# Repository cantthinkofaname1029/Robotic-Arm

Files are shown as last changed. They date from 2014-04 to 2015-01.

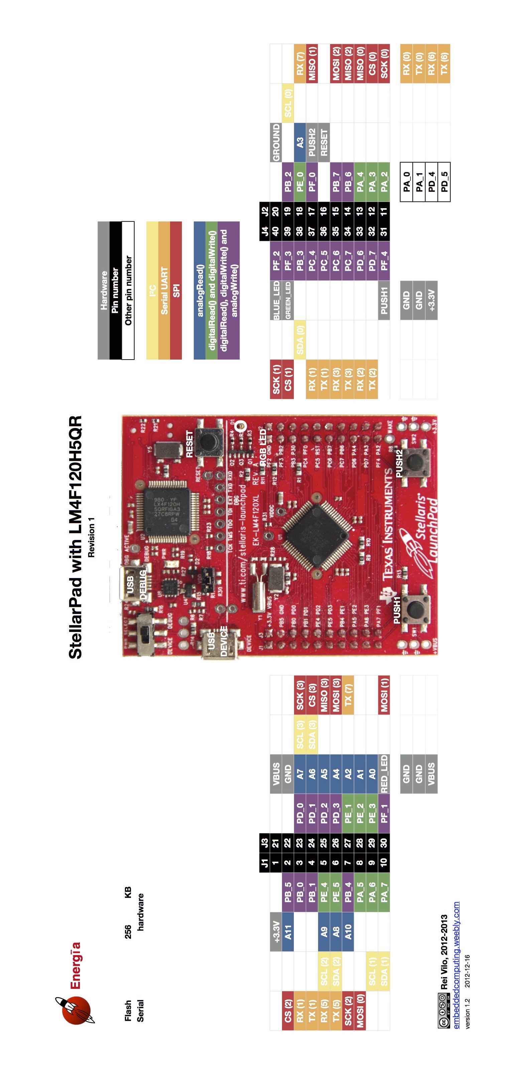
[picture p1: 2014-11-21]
hardware/v4/StellarPadLM4F120H5QR-V1.0.jpg

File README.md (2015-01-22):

Robotic Arm
===========

2015 Robotic Arm Hardware/Software
- Please see the wiki for more information about the subjects below.

Hardware:
---------

###PCBs
-Version 3 of the arm board aka "the old-new arm board" is a remake of V2 (the old arm board currently on Phoenix). It is designed to have the exact same functionality as Phoenix, without using a master-slave protocol. It features a TI Launchpad Stellaris as the central CPU, 3 motor controllers that can connect to up to two motors each, and an RS-485 connection to the old dynamixel (MX-64R). It has the additional capability of communicating with the end effector via XBee and receives power from PORN.

-Version 4 of the arm board aka "the illuminati board" is the latest version. It features a TIVA-C for it's central processor and extends the functionality of Version 3. It only has one motor controller for the Pololu actuator, but it connects to multiple Dynamixels over TTL. There is a 9DOF IMU added on the board for additional control capabilities. it also receives power from PORN.

###Motors
-The base of the arm as well as the elbow joints use the Dynamixel MX-64T. It operates at a MAXIMUM voltage of 14.8V. Information on these motors can be found here:

http://support.robotis.com/en/product/dynamixel/mx_series/mx-64.htm

http://support.robotis.com/en/techsupport_eng.htm#product/dynamixel/mx_series/mx-64.htm

http://support.robotis.com/en/techsupport_eng.htm#software/dynamixelsdk.htm

-The wrist joints on the arm use the Dynamixel MX-28T. It operates at a MAXIMUM voltage of 14.8V. Information on these motors can be found here:

http://support.robotis.com/en/product/dynamixel/mx_series/mx-28.htm

http://support.robotis.com/en/techsupport_eng.htm#product/dynamixel/mx_series/mx-28.htm

http://support.robotis.com/en/techsupport_eng.htm#software/dynamixelsdk.htm

-The shoulder joint of the arm uses a Pololu Linear Actuator with an 8" stroke and a potentiometer for feedback. It operates at a MAXIMUM of 12V. It will be controlled using an on-board motor controller. Information on this actuator can be found here:

https://www.pololu.com/product/2337/specs

Software:
---------

-Software for V3 is nearing completion. It will have basic functionality for the arm for open-loop controls.

-Software for V4 has not started yet. It will be a port from the V3 code to TivaWare.

-After the V4 code has been completed for basic functionality, we need to start writing the framework for more exotic control methods.

-There is a Dynamixel SDK found here:

http://support.robotis.com/en/software/dynamixelsdk.htm

-There is a fully-written Dynamixel Library written for Arduino here:

http://savageelectronics.blogspot.com/2011/01/arduino-y-dynamixel-ax-12.html

if you can't read spanish or use google translate, the various libraries are found here:

http://savageelectronics.blogspot.com/2011/08/actualizacion-biblioteca-dynamixel.html

These will probably be useful to us when writing the further code.

-We may have to write our own PID control for the actuator in the future. Get an introduction to PID for arduino here:

http://brettbeauregard.com/blog/2011/04/improving-the-beginners-pid-introduction/

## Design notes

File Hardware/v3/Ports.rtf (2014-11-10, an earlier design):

Motor Controller 1
Enable A PE1
A_1 PD1
A_2 PA2
Enable B PE2
B_1 PD2
B_2 PD3
Motor Controller 2
Enable A PB7
A_1 PE0
A_2 PF0
Enable B PB2
B_1 PF2
B_2 PF3
Motor Controller 3
Enable A PB6
A_1 PA3
A_2 PA4
Rovecom
RX(3) PC6
TX(3) PC7
End Effector
RX(2) PD6
TX(2) PD7
Dynamxiel
Data Control PB3
RX(1) PC4
TX(1) PC5

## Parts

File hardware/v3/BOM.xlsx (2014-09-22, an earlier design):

Name | Part Number | Type of Component | Quantity | Unit Price | Price | Company | Website
.1uF capictor |  | Passive SMD 603 | 13 |  | $0.00
1N4148 |  | Diode | 6 | $0.10 | $0.60 | Digikey | http://www.digikey.com/product-detail/en/1N4148TA/1N4148TACT-ND/1532747
5mm Terminal |  | Power Connector | 6 |  | $0.00
1kΩ |  | Passive SMD 603 | 5 |  | $0.00
5.6nF capictor |  | Passive SMD 603 | 5 | $0.10 | $0.50 | Digikey | http://www.digikey.com/product-detail/en/CL10B562KB8SFNC/1276-2092-1-ND/3890178
100kΩ resistor |  | Passive SMD 603 | 4 |  | $0.00
120Ω |  | Passive SMD 603 | 4 |  | $0.00
100Ω resistor |  | Passive SMD 603 | 3 |  | $0.00
10nF capictor |  | Passive SMD 603 | 3 | $0.10 | $0.30 | Digikey | http://www.digikey.com/product-detail/en/C0603C103K5RACTU/399-1091-1-ND/411366
220nF capictor |  | Passive SMD 603 | 3 | $0.10 | $0.30 | Digikey | http://www.digikey.com/product-detail/en/C1608X7R1H223K080AA/445-1312-1-ND/567696
Green LED |  | SMD LED | 3 | $2.95 | $2.95 | Sparkfun | https://www.sparkfun.com/products/11169
L6206D |  | IC | 3 | $10.64 | $31.92 | Digikey | http://www.digikey.com/product-detail/en/L6206D/497-3999-5-ND/725434
LTC490 |  | IC | 2 | $4.82 | $9.64 | Digikey | http://www.digikey.com/product-detail/en/LTC490CN8%23PBF/LTC490CN8%23PBF-ND/891732
Vertical RJ45 |  | Connector | 2 |  | $0.00
Red LED |  | SMD LED | 2 | $2.95 | $2.95 | Sparkfun | https://www.sparkfun.com/products/11248
XBEE Headers |  | SMD Headers | 2 | $0.95 | $1.90 | Sparkfun | https://www.sparkfun.com/products/10030
XBEE |  | Wireless | 2 | $24.95 | $49.90 | Sparkfun | https://www.sparkfun.com/products/11215
12V LDO |  | LDO | 2 | $0.70 | $1.40 | Digikey | http://www.digikey.com/product-search/en?KeyWords=MC7812BTG&WT
220Ω |  | Passive SMD 603 | 1 |  | $0.00
MAX485 |  | IC | 1 | $2.65 | $2.65 | Digikey | http://www.digikey.com/product-detail/en/MAX485CPA%2B/MAX485CPA%2B-ND/948026
Launchpad |  | Processor | 1 | $13.02 | $13.02 | Newark | http://www.newark.com/texas-instruments/ek-tm4c123gxl/eval-board-tm4c123g-tiva-c-launchpad/dp/73W9275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
XBEE Explorer |  | Wireless | 1 | $9.95 | $9.95 | Sparkfun | https://www.sparkfun.com/products/11373
18V LDO |  | LDO | 1 | $0.57 | $0.57 | Digikey | http://www.digikey.com/product-search/en?vendor=0&keywords=MC7818BTG
5V LDO |  | LDO | 1 | $0.48 | $0.48 | Digikey | http://www.digikey.com/product-detail/en/MC78M05CDTRKG/MC78M05CDTRKGOSCT-ND/1139757
3.3V LDO |  | LDO | 1 | $0.90 | $0.90 | Digikey | http://www.digikey.com/product-detail/en/MC33269DT-3.3G/MC33269DT-3.3GOS-ND/1479177
 |  |  |  |  | $129.93

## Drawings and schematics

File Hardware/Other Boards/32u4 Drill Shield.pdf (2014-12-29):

1.25

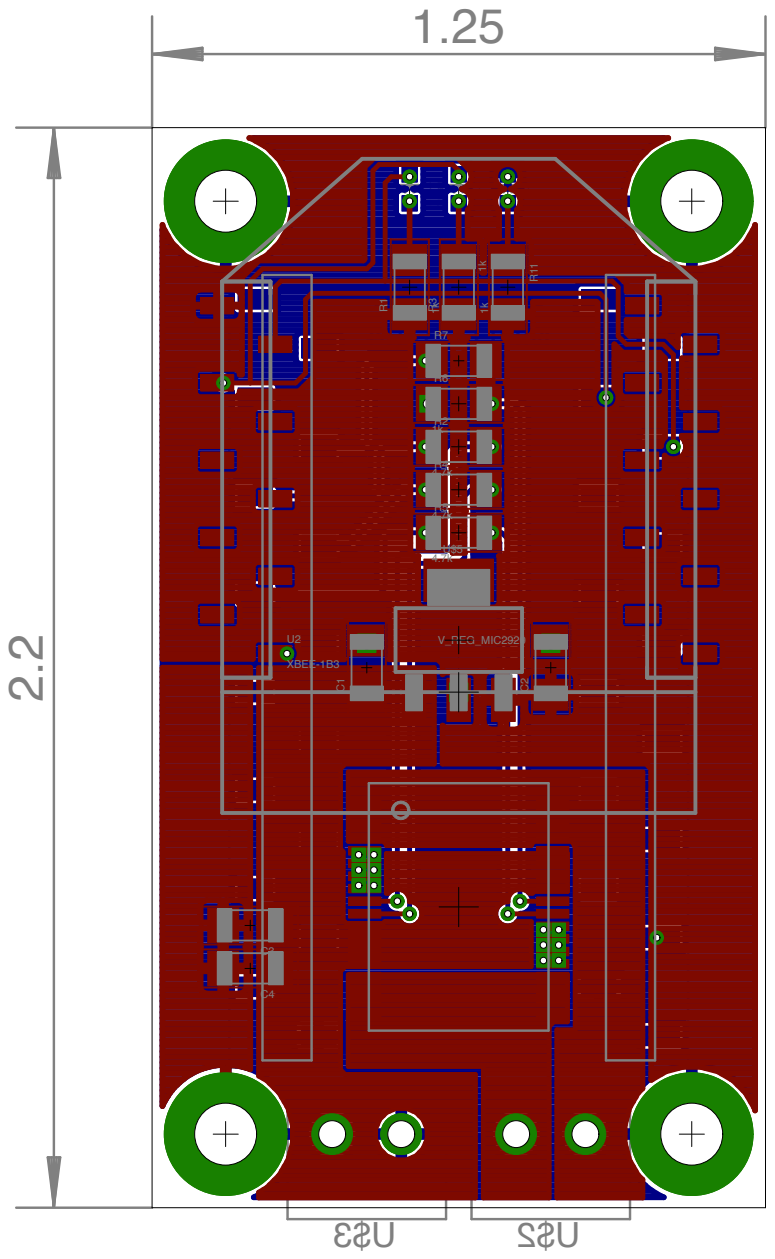
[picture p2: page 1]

R2
1k

R5
4.7k

V_REG_MIC2920

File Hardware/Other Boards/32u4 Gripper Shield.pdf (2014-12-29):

1.25

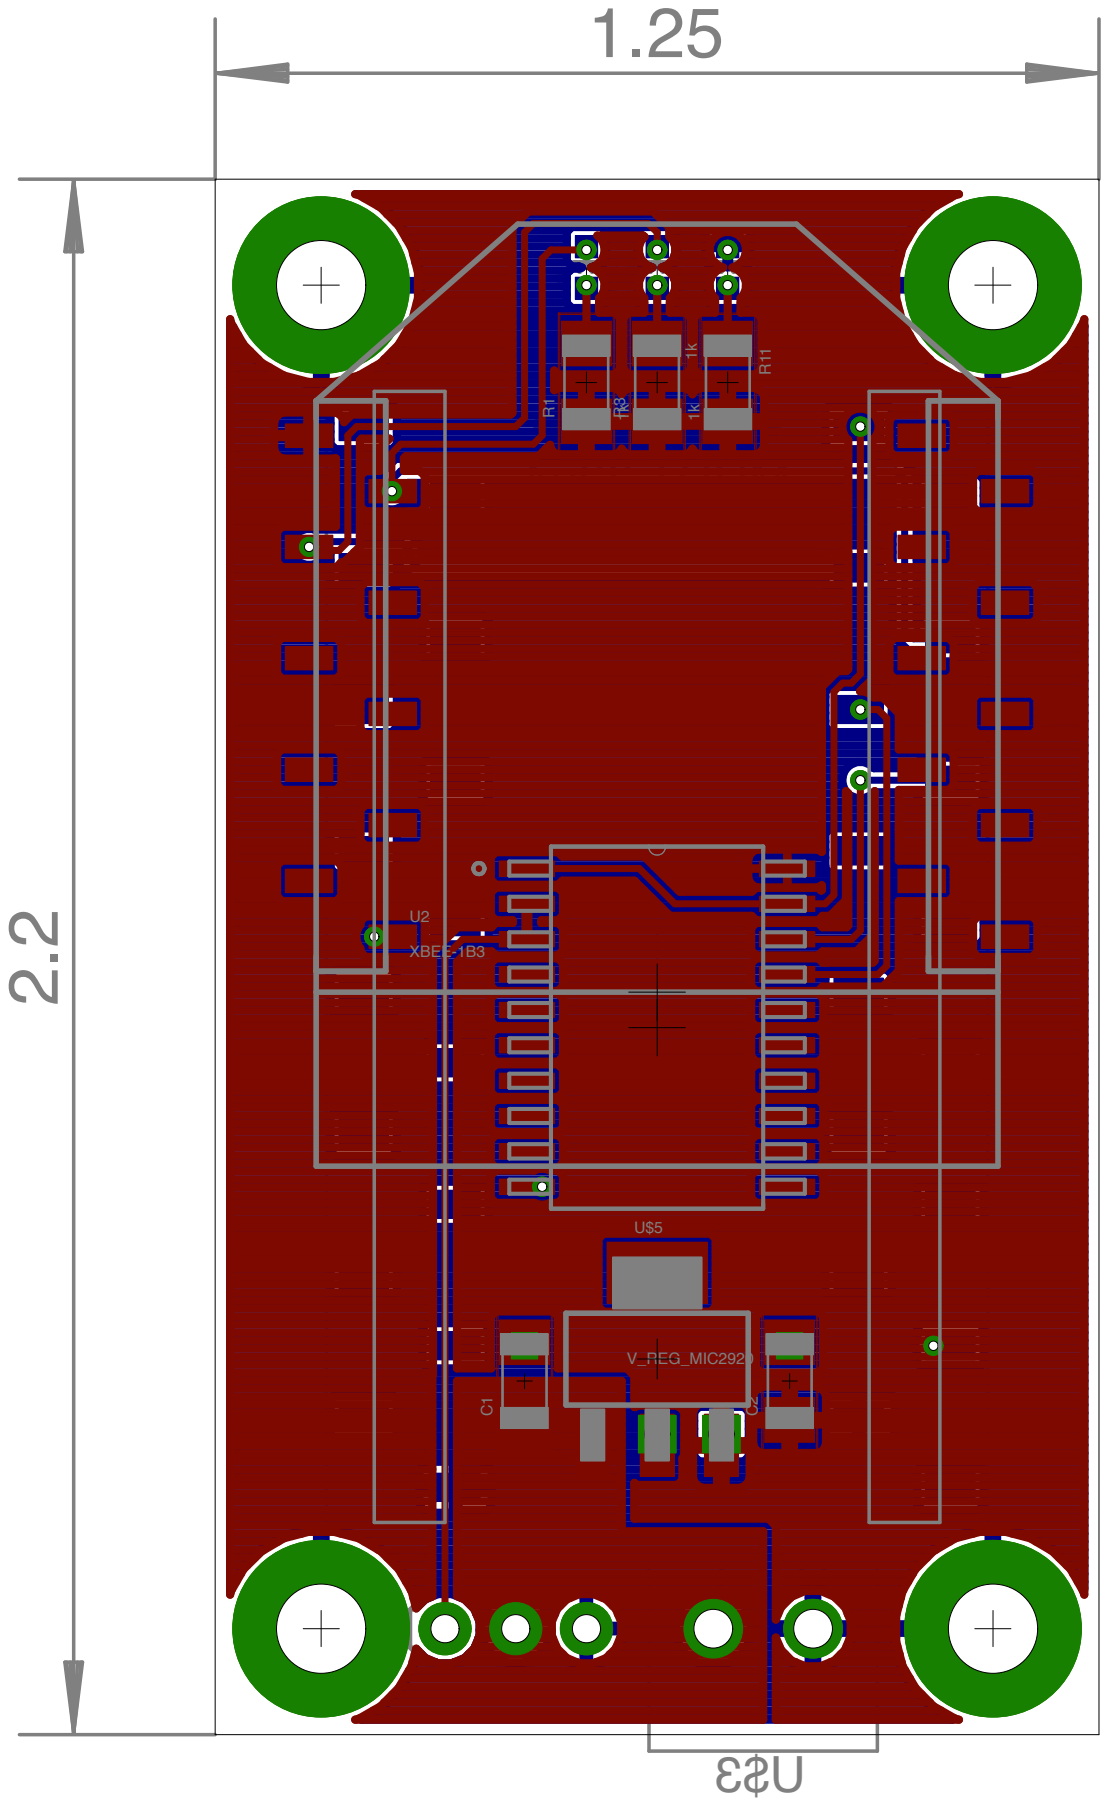
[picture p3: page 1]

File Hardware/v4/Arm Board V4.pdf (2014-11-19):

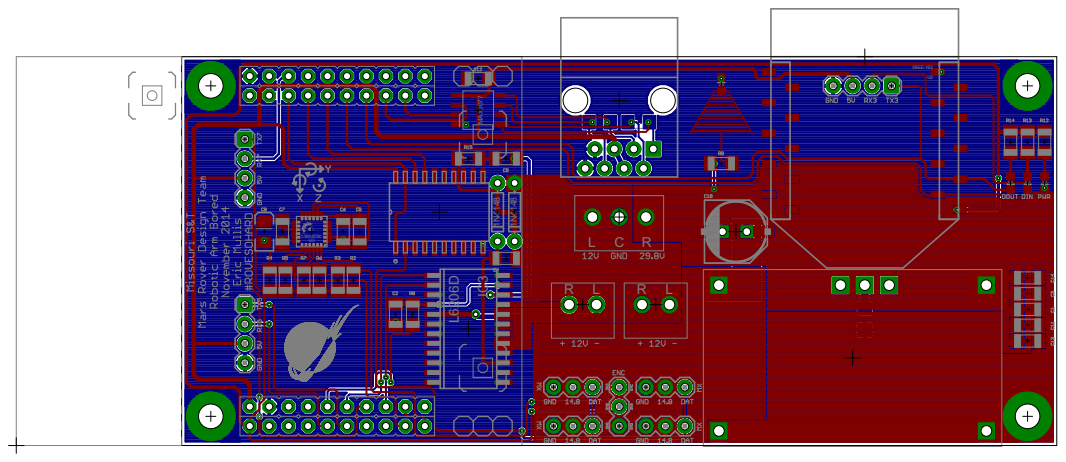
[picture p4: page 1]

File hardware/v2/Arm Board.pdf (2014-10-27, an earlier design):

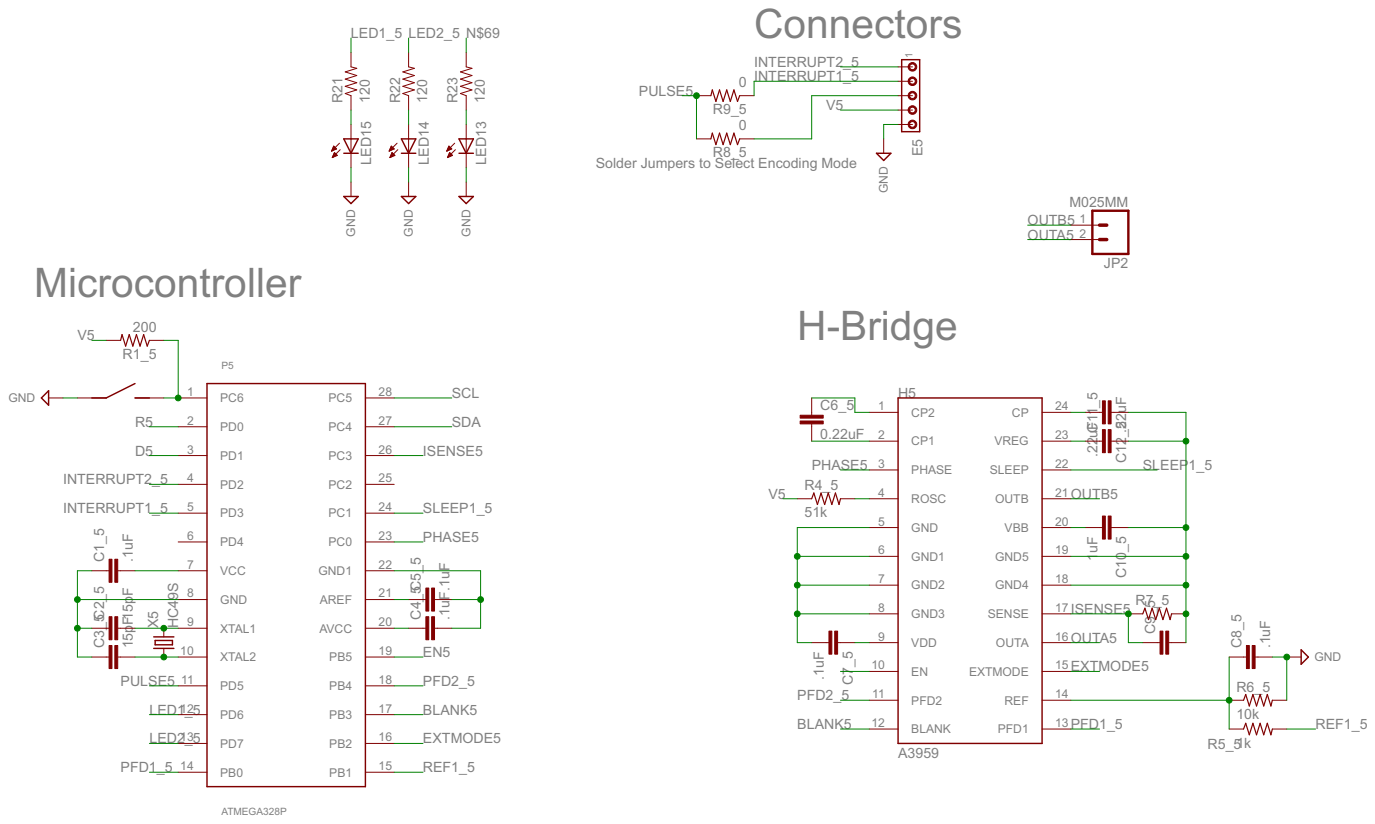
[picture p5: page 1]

Solder Jumpers to Select Encoding Mode

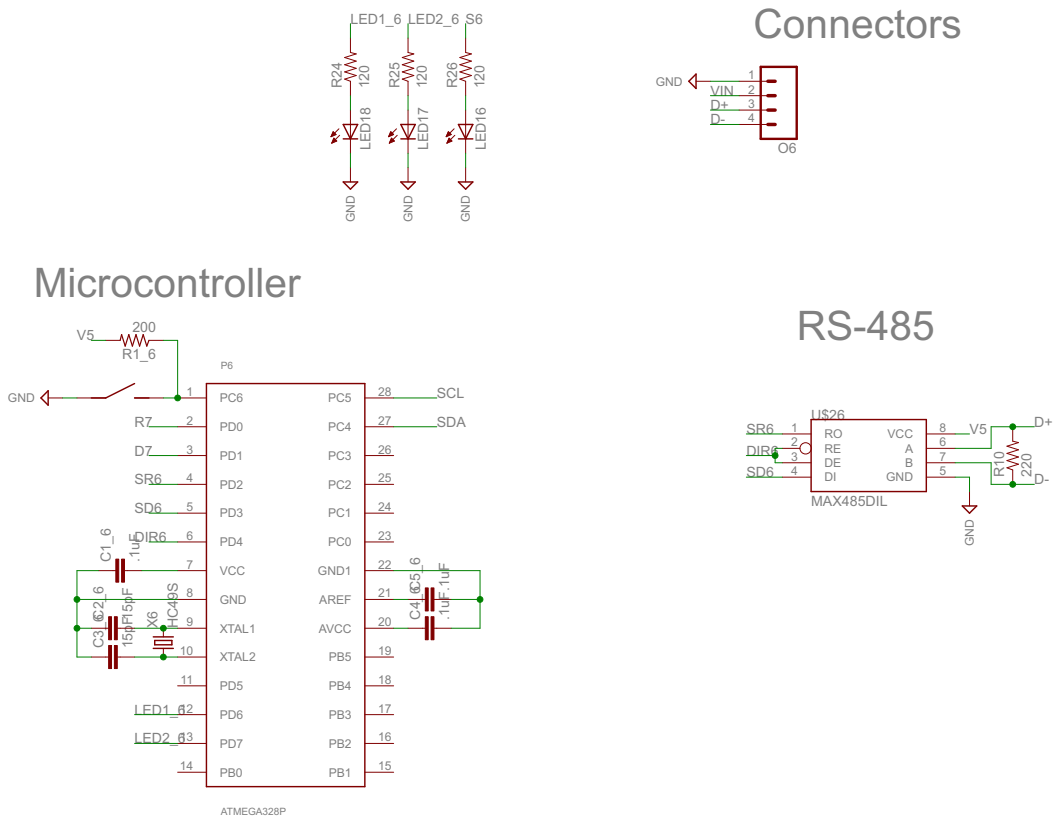
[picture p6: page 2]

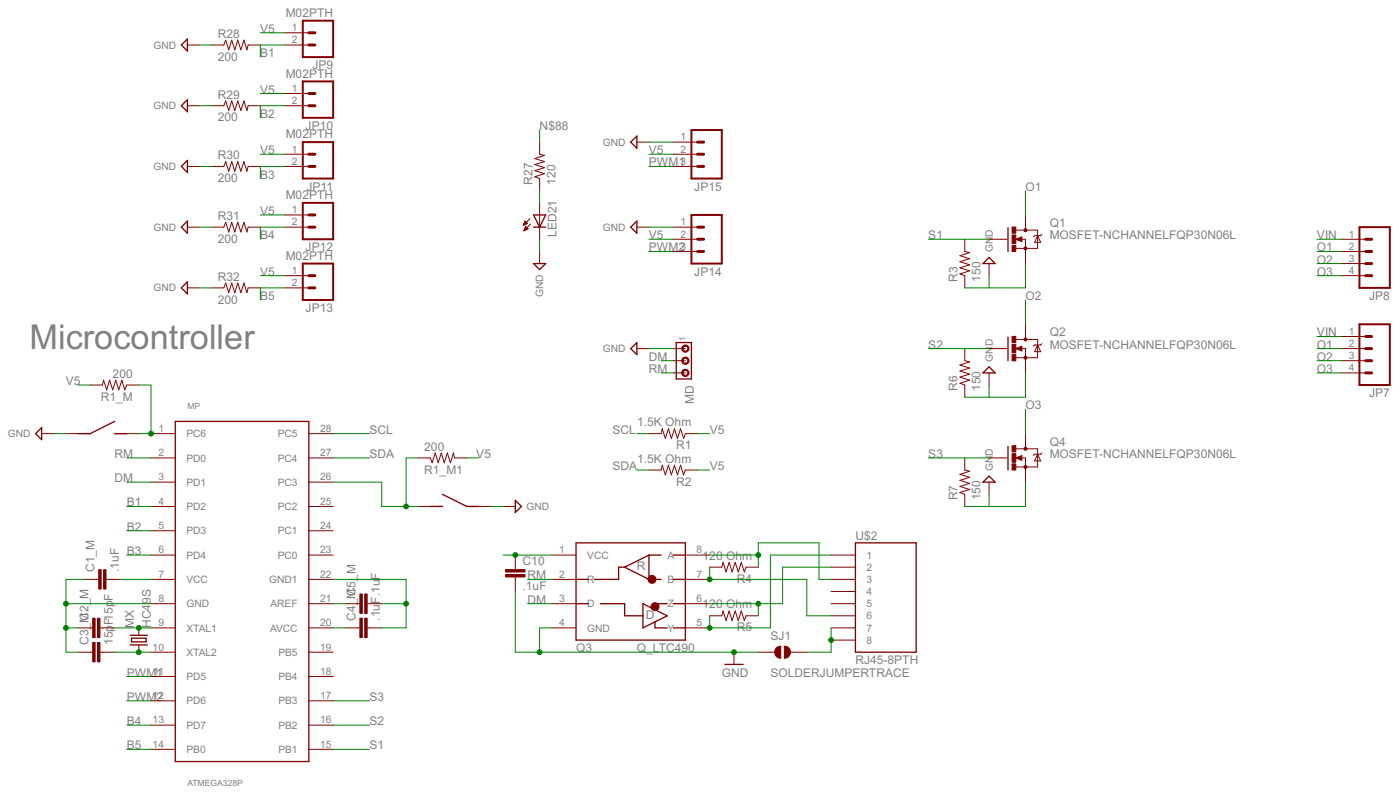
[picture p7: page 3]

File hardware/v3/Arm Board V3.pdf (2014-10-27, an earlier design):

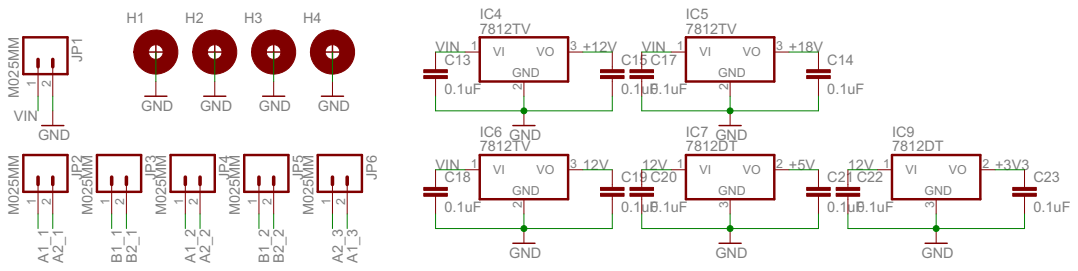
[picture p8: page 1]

M025MM GND M025MM M025MM M025MM M025MM M025MM GND GND GND GND 7812TVGND 7812TVGND 0.1uF 0.1uF0.1uF 0.1uF GND 0.1uF 0.1uF 7812TV GND 0.1uF 0.1uF 7812DT GND 0.1uF 0.1uF 7812DT JP1 12 JP2 12 JP3 12 JP4 12 JP5 12 JP6 12 H1 H2 H3 H4 IC4 GND VI 1 2 VO 3 IC5 GND VI 1 2 VO 3 C13 C15 C17 C14 C18 C19 IC6 GND VI 1 2 VO 3 C20 C21 IC7 GND VI 1 3 VO 2 C22 C23 IC9 GND VI 1 3 VO 2 A1_1 A2_1 B1_1 B2_1 A1_2 A2_2 B1_2 B2_2 A2_3 VIN VIN VIN VIN A1_3 +12V +18V 12V 12V +5V 12V +3V3

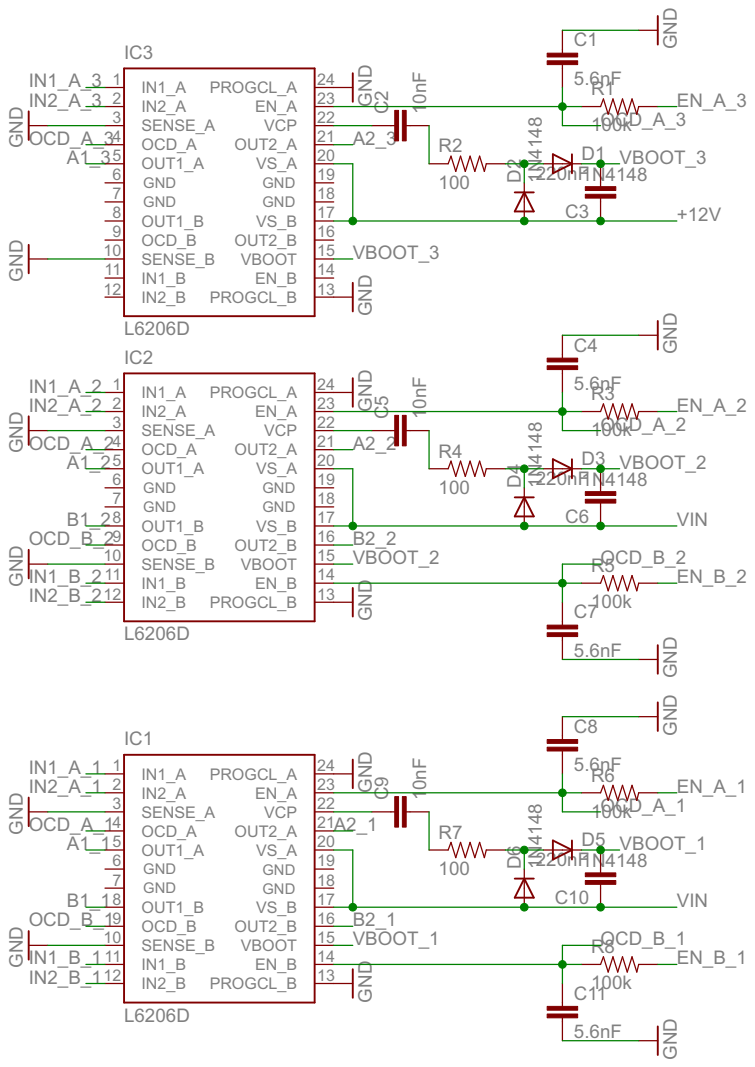
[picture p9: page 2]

GND GND
OCD_A_3

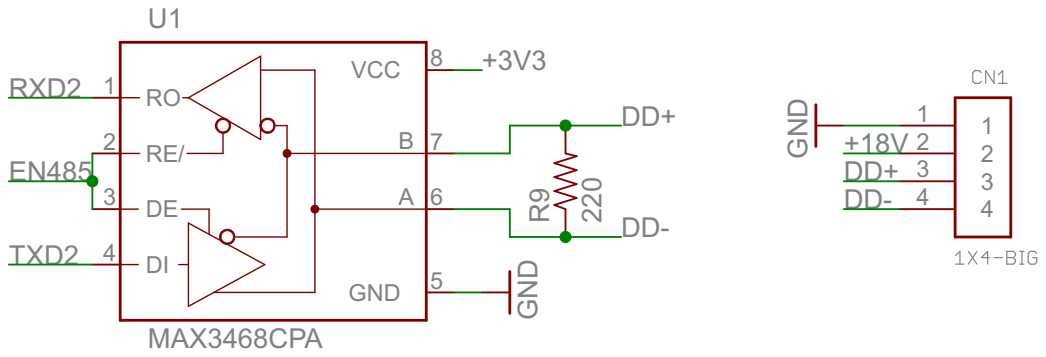
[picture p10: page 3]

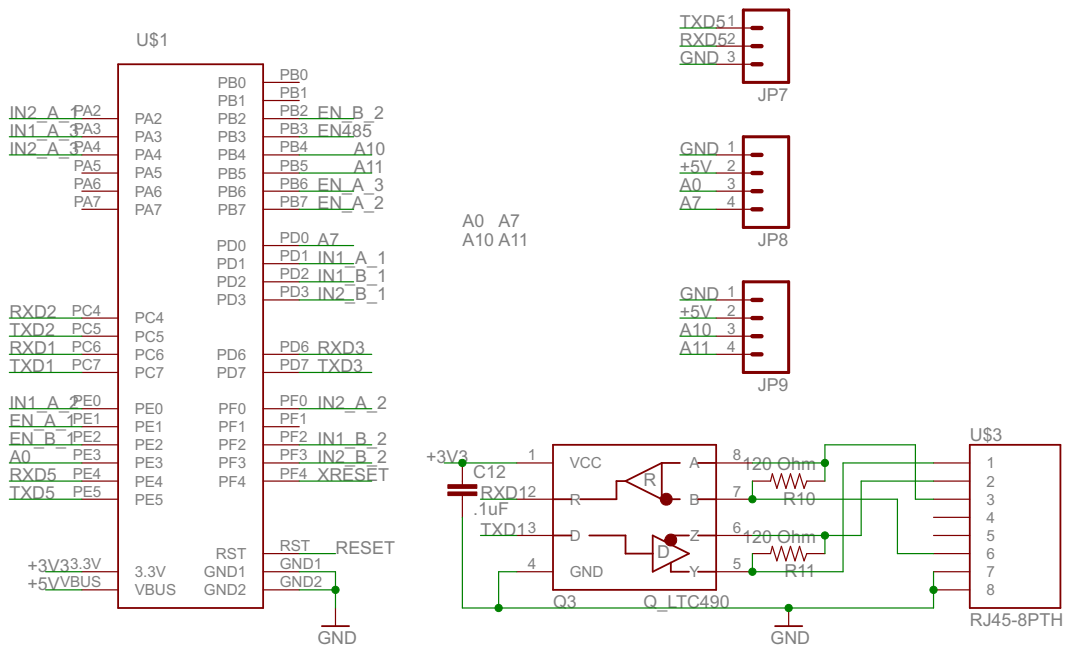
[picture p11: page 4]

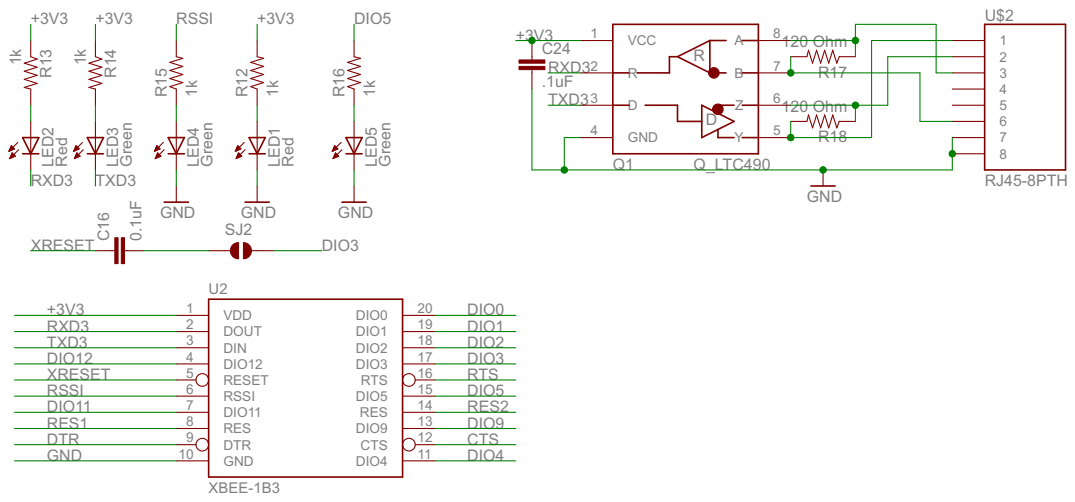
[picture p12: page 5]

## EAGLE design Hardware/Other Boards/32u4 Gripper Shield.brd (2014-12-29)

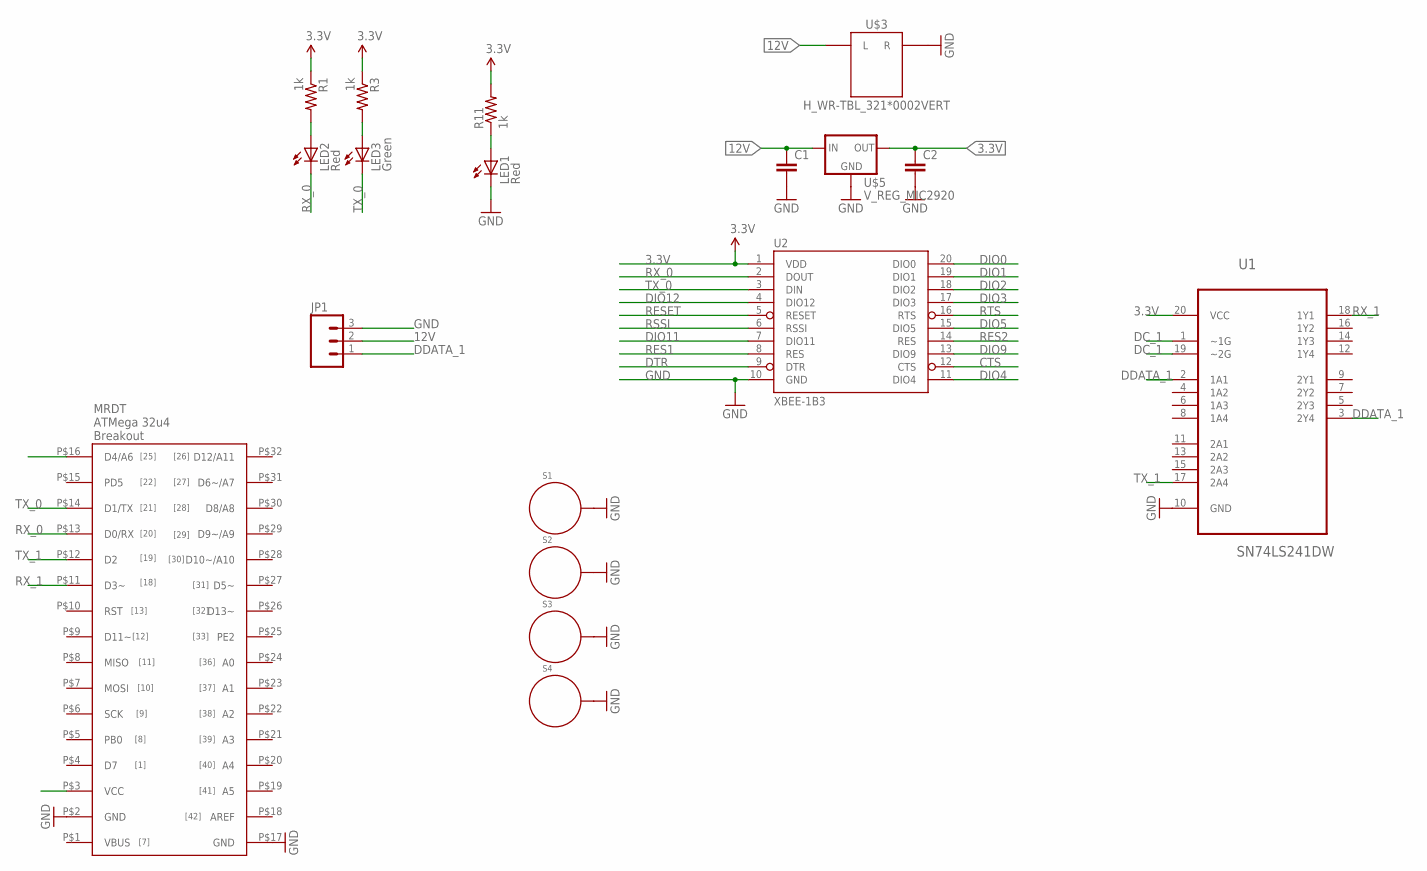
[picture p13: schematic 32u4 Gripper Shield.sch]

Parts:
C1, C2: CAP1206; 1206
JP1: M03PTH; 1X03
LED1, LED2: Red; LED-0603
LED3: Green; LED-0603
R1, R3, R11: 1k; 1206
S1, S2, S3, S4: STANDOFF_ELECTRICAL; STANDOFF-ELECTRICAL
U1: SN74LS241DW; SOIC127P1030X265-20N
U2: XBEE-1B3; XBEE-SMD
U$1: 32U4_BREAKOU_SMD; 32U3_MCU_DIP_SMD
U$3: H_WR-TBL_321*0002VERT; 691321100002
U$5: V_REG_MIC2920; SOT223

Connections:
3.3V: C2.1, R1.1, R3.1, R11.2, U1.20 (VCC), U2.1 (VDD), U$1.P$3 (VCC), U$5.3 (OUT)
12V: C1.1, JP1.2, U$3.L, U$5.1 (IN)
CTS: U2.12 (CTS)
DC_1: U1.1 (~1G), U1.19 (~2G), U$1.P$16 (D4/A6)
DDATA_1: JP1.1, U1.2 (1A1), U1.3 (2Y4)
DIO0: U2.20 (DIO0)
DIO1: U2.19 (DIO1)
DIO2: U2.18 (DIO2)
DIO3: U2.17 (DIO3)
DIO4: U2.11 (DIO4)
DIO5: U2.15 (DIO5)
DIO9: U2.13 (DIO9)
DIO11: U2.7 (DIO11)
DIO12: U2.4 (DIO12)
DTR: U2.9 (DTR)
GND: C1.2, C2.2, JP1.3, LED1.C, S1.P1, S2.P1, S3.P1, S4.P1, U1.10 (GND), U2.10 (GND), U$1.P$2 (GND), U$1.P$17 (GND), U$3.R, U$5.2 (GND), U$5.4 (GND)
unnamed: LED2.A, R1.2
unnamed: LED3.A, R3.2
unnamed: LED1.A, R11.1
RES1: U2.8 (RES)
RES2: U2.14 (RES)
RESET: U2.5 (RESET)
RSSI: U2.6 (RSSI)
RTS: U2.16 (RTS)
RX_0: LED2.C, U2.2 (DOUT), U$1.P$13 (D0/RX)
RX_1: U1.18 (1Y1), U$1.P$11 (D3~)
TX_0: LED3.C, U2.3 (DIN), U$1.P$14 (D1/TX)
TX_1: U1.17 (2A4), U$1.P$12 (D2)

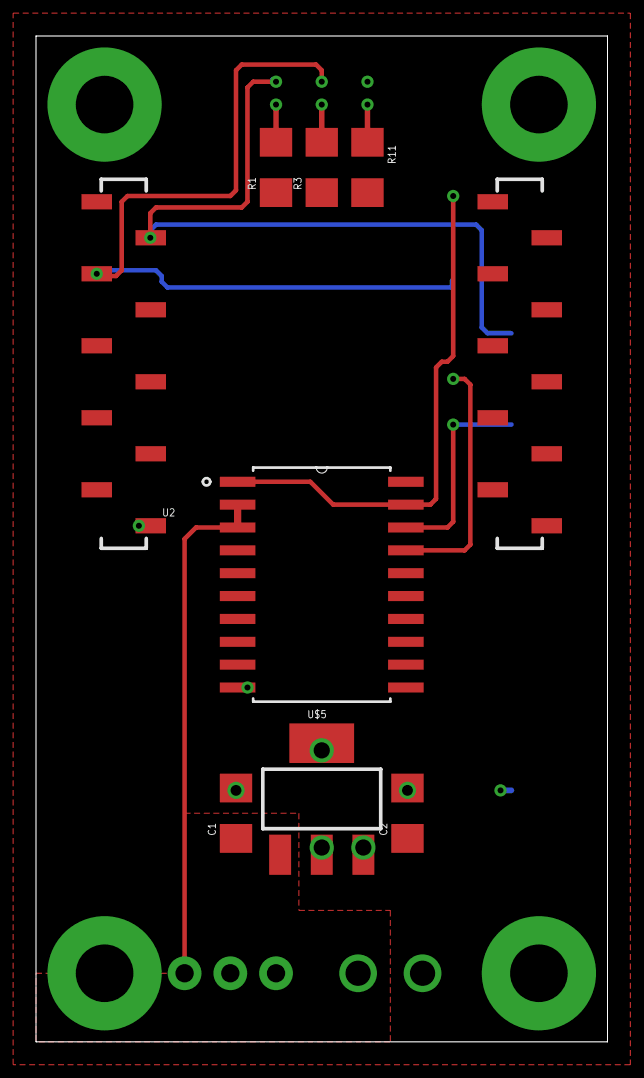
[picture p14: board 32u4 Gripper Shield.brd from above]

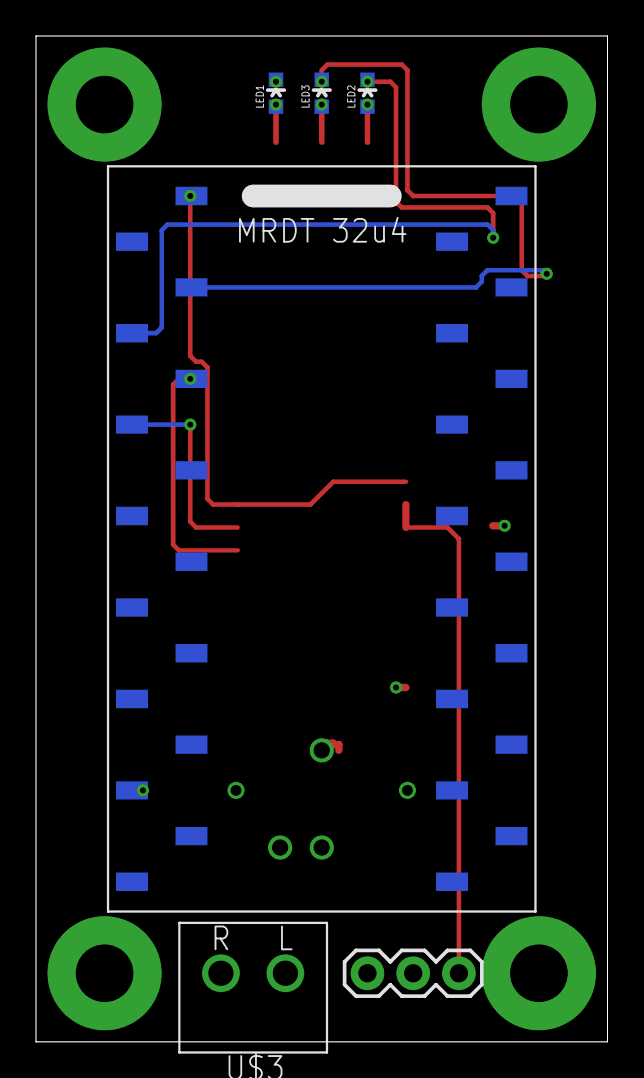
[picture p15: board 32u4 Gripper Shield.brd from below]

Board: 2 copper layers, 31.8 x 55.9 mm, 18 parts (6 on the bottom side), 12 nets.

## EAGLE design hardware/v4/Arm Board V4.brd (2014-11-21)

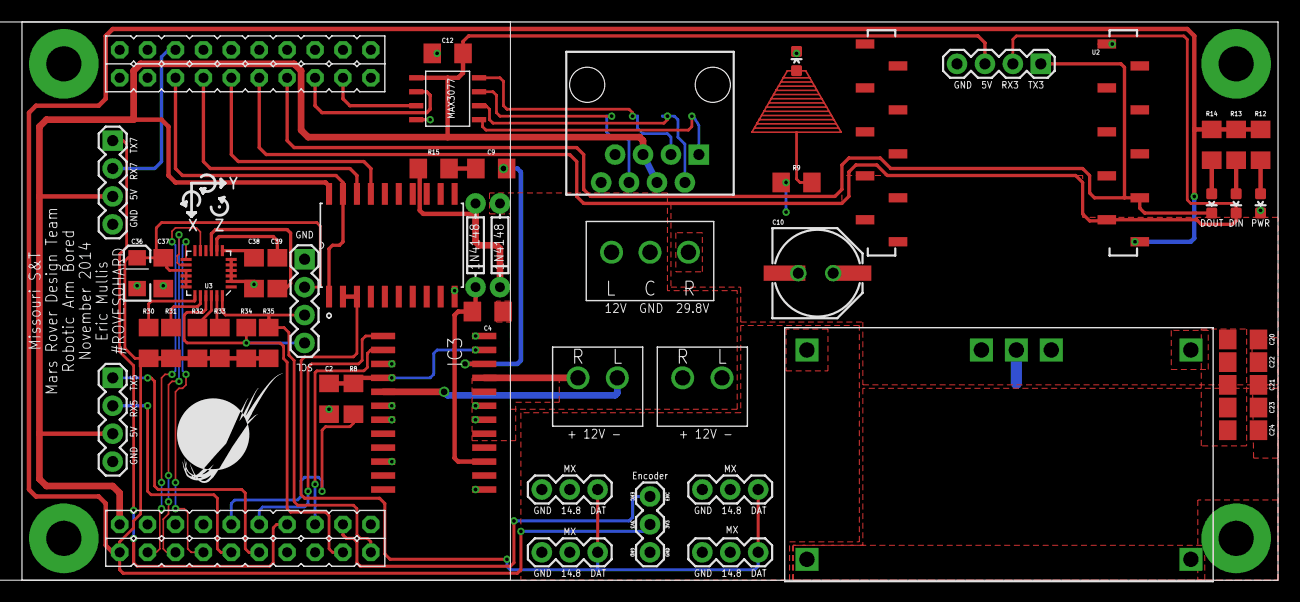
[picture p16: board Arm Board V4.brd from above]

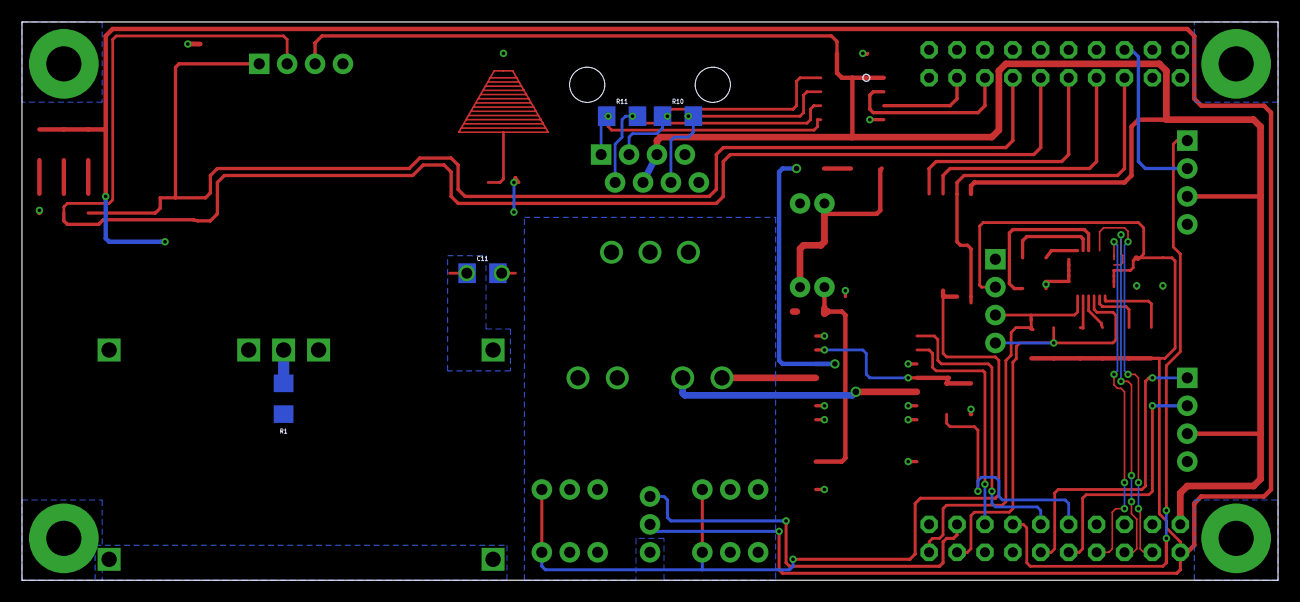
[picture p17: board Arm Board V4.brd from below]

Board: 2 copper layers, 114.3 x 50.8 mm, 60 parts (4 on the bottom side), 50 nets.

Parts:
C2: 5.6nF; 1206
C4: 220nF; 1206
C9: 10nF; 1206
C10: 330uF; PANASONIC_E
C11, C20: 1.0uF; 1206
C12: .1uF; 1206
C21, C22, C23, C24, C38: 4.7uF; 1206
C36: 10uF; EIA3216
C37: 1uF; 1206
C39: .22uF; 1206
D1, D2: 1N4148; DIODE-1N4148
IC3: L6206D; SO24
JP1, JP2, JP3, JP4: 1X04
JP7, JP9, JP10, JP11, JP12: 1X03
LED1, LED2, LED5: RED; LED-0603
LED3: GREEN; LED-0603
P1: STELLARIS-LAUNCHPADSTELLARIS-LAUNCHPAD-XL; LAUNCHPAD-XL
R1: 17.2k; 1206
R8: 100k; 1206
R9: 1.5k; 1206
R10, R11: 120 Ohm; 1206
R12, R13, R14: 1k; 1206
R15: 100; 1206
R30, R31, R32, R33, R34, R35: 10k; 1206
S1, S2, S3, S4: STANDOFF_ELECTRICAL; STANDOFF-ELECTRICAL
U1: SN74LS241DW; SOIC127P1030X265-20N
U2: XBEE-1B3; XBEE-SMD
U3: LSM9DS0; LGA-24
U$2: Q_PTN78020; R_PDSS-T7
U$3: RJ45-8PTH; RJ45-8
U$4: MAX3077; MAX3070E
U$5: 691321100003; 691322110003
U$6, U$7: H_WR-TBL_321*0002VERT; 691321100002

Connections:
14.8V: C10.+, C11.1, JP9.2, JP10.2, JP11.2, JP12.2, U$2.6
+3V3: C36.A, C37.1, JP4.2, JP7.2, P1.3.3V, R12.2, R13.1, R14.1, R30.2, R31.2, R32.2, R33.2, R34.2, R35.2, U2.1, U3.15, U3.16, U3.17, U3.18
+5V: C12.1, JP1.3, JP2.3, JP3.3, P1.VBUS, U1.20, U$3.4, U$3.5, U$4.VCC
+12V: C4.1, D2.A, IC3.17, IC3.20, U$5.L, U$7.L
A1: IC3.5, U$6.L
A2: IC3.21, U$6.R
CS_G: R30.1, U3.19
CS_XM: R31.1, U3.20
DC_1: P1.PB3, U1.1, U1.19
DDATA_1: JP9.3, JP10.3, JP11.3, JP12.3, U1.2, U1.3
EN_A: P1.PD2, R8.2
GND: C2.1, C10.-, C11.2, C12.2, C20.2, C21.2, C22.2, C23.2, C24.2, C36.C, C37.2, C38.2, IC3.3, IC3.6, IC3.7, IC3.10, IC3.13, IC3.18, IC3.19, IC3.24, JP1.4, JP2.4, JP3.4, JP4.1, JP7.1, JP9.1, JP10.1, JP11.1, JP12.1, LED1.C, LED5.C, P1.GND1, P1.GND2, R1.1, S1.P1, S2.P1, S3.P1, S4.P1, U1.10, U2.10, U3.2, U3.3, U3.4, U3.5, U3.6, U$2.1, U$2.7, U$3.7, U$3.8, U$4.GND, U$5.C, U$7.R
IN1_A: IC3.1, P1.PD3
IN2_A: IC3.2, P1.PE2
INT1_XM: P1.PB1, U3.13
INT2_XM: P1.PB0, U3.14
INT_G: P1.PB5, U3.11
LA_ENC: JP7.3, P1.PE3
unnamed: R11.1, U$3.2, U$4.Z
unnamed: R10.2, U$3.6, U$4.B
unnamed: R10.1, U$3.3, U$4.A
unnamed: LED2.A, R13.2
unnamed: R11.2, U$3.1, U$4.Y
unnamed: LED3.A, R14.2
unnamed: R1.2, U$2.4
unnamed: C39.1, U3.9
unnamed: C39.2, U3.8
unnamed: C38.1, U3.7
unnamed: LED5.A, R9.1
unnamed: D1.A, D2.C, R15.2
unnamed: C9.2, R15.1
unnamed: C9.1, IC3.22
unnamed: LED1.A, R12.1
OCD_A: C2.2, IC3.4, IC3.23, R8.1
RX_1: P1.PC4, U1.18
RX_2: P1.PD6, U$4.RO
RX_3: JP1.2, LED2.C, P1.PC6, U2.2
RX_5: JP3.2, P1.PE4
RX_7: JP2.2, P1.PE0
SCL: JP4.4, P1.PA6, R34.1, U3.21
SDA: JP4.3, P1.PA7, R35.1, U3.24
SDO_G: R32.1, U3.22
SDO_XM: R33.1, U3.23
TX_1: P1.PC5, U1.17
TX_2: P1.PD7, U$4.DI
TX_3: JP1.1, LED3.C, P1.PC7, U2.3
TX_5: JP3.1, P1.PE5
TX_7: JP2.1, P1.PE1
VBOOT: C4.2, D1.C, IC3.15
VIN: C20.1, C21.1, C22.1, C23.1, C24.1, R9.2, U$2.2, U$5.R

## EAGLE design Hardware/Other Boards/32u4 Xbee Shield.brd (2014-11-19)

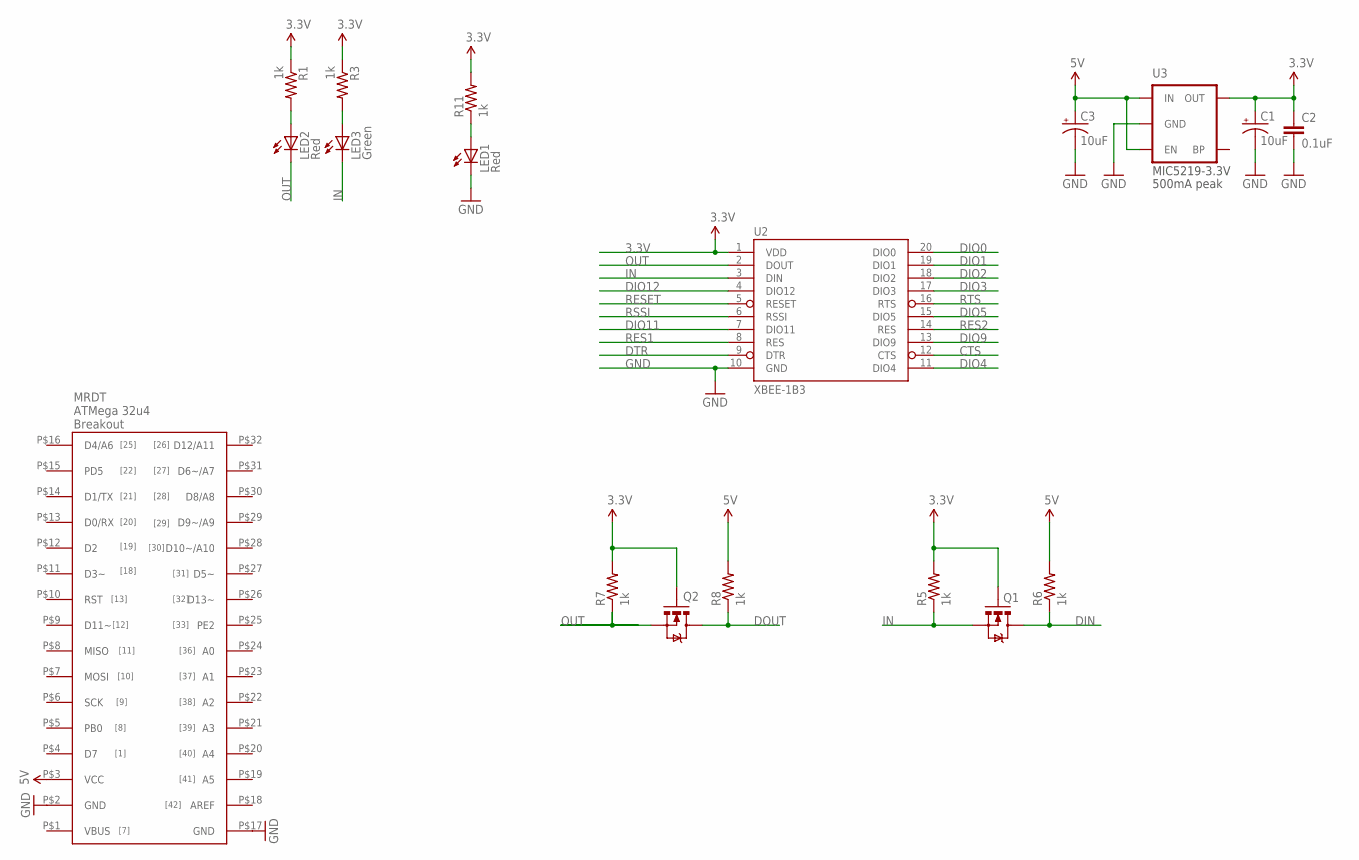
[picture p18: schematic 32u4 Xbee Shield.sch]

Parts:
C1, C3: 10uF; EIA3216
C2: 0.1uF; 1206
LED1, LED2: Red; LED-0603
LED3: Green; LED-0603
Q1, Q2: MOSFET-NCHANNELSMD; SOT23-3
R1, R3, R5, R6, R7, R8, R11: 1k; 1206
U2: XBEE-1B3; XBEE-SMD
U3: V_REG_LDOSMD; SOT23-5
U$1: 32U4_BREAKOU_SMD; 32U3_MCU_DIP_SMD

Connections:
3.3V: C1.A (+), C2.1, Q1.1 (G), Q2.1 (G), R1.1, R3.1, R5.2, R7.2, R11.2, U2.1 (VDD), U3.5 (OUT)
5V: C3.A (+), R6.2, R8.2, U3.1 (IN), U3.3 (EN), U$1.P$3 (VCC)
CTS: U2.12 (CTS)
DIN: Q1.3 (D), R6.1
DIO0: U2.20 (DIO0)
DIO1: U2.19 (DIO1)
DIO2: U2.18 (DIO2)
DIO3: U2.17 (DIO3)
DIO4: U2.11 (DIO4)
DIO5: U2.15 (DIO5)
DIO9: U2.13 (DIO9)
DIO11: U2.7 (DIO11)
DIO12: U2.4 (DIO12)
DOUT: Q2.3 (D), R8.1
DTR: U2.9 (DTR)
GND: C1.C (-), C2.2, C3.C (-), LED1.C, U2.10 (GND), U3.2 (GND), U$1.P$2 (GND), U$1.P$17 (GND)
IN: LED3.C, Q1.2 (S), R5.1, U2.3 (DIN)
unnamed: LED2.A, R1.2
unnamed: LED3.A, R3.2
unnamed: LED1.A, R11.1
OUT: LED2.C, Q2.2 (S), R7.1, U2.2 (DOUT)
RES1: U2.8 (RES)
RES2: U2.14 (RES)
RESET: U2.5 (RESET)
RSSI: U2.6 (RSSI)
RTS: U2.16 (RTS)

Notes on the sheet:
MIC5219-3.3V
500mA peak

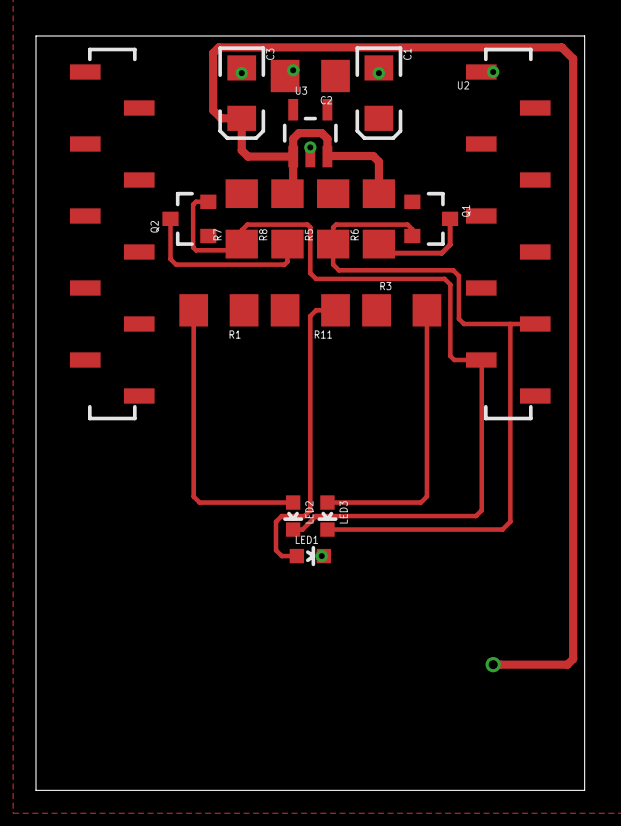
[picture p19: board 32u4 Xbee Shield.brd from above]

Board: 2 copper layers, 30.5 x 41.9 mm, 18 parts (1 on the bottom side), 10 nets.

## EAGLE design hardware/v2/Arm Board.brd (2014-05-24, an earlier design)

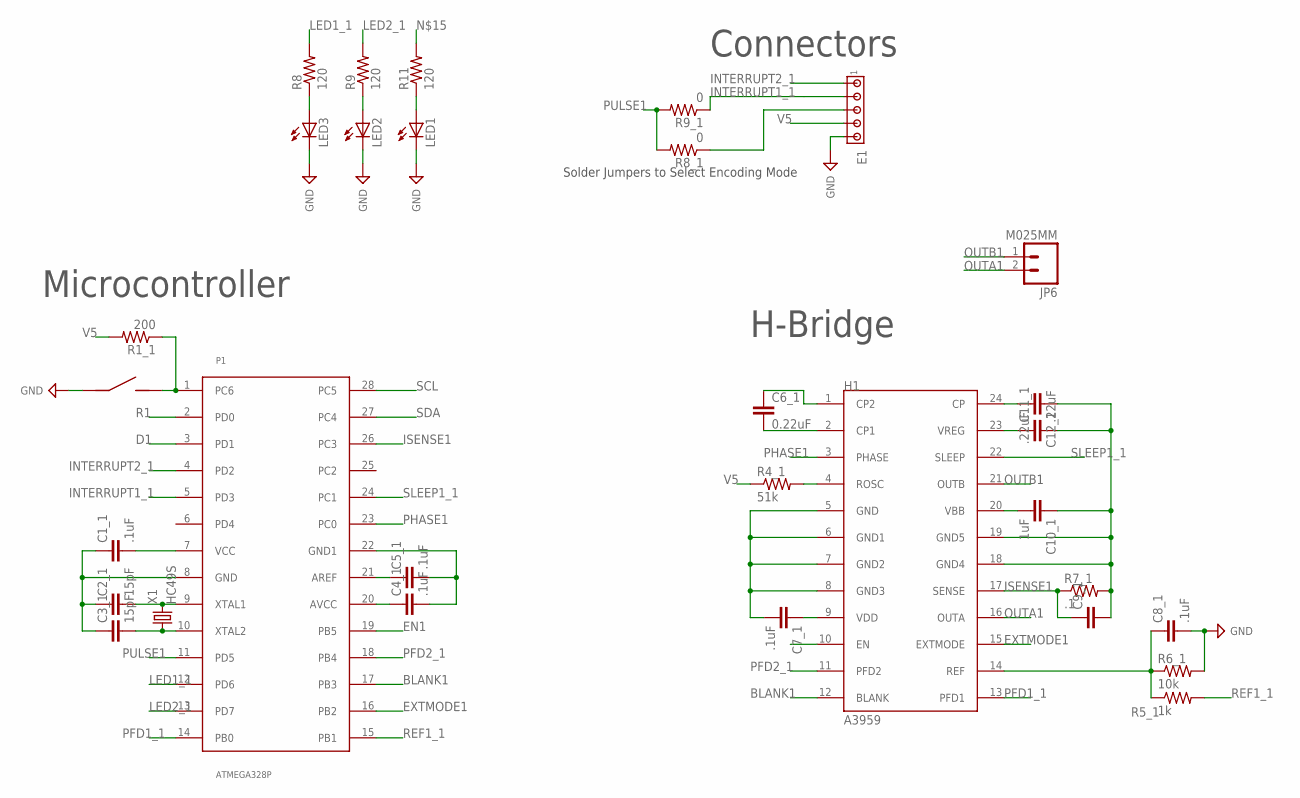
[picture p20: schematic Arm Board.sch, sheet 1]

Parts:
C1_1, C4_1, C5_1, C7_1, C8_1: .1uF; C_0805
C2_1, C3_1: 15pF; C_0805
C6_1: 0.22uF; C_0805
C9_1: C_CAP_0805; C_0805
C10_1: 1uF; C_0805
C11_1, C12_1: .22uF; C_0805
E1: J_MTA5P_100; J_MTA100_5P
H1: A3959; DIP24
JP6: M025MM; SCREWTERMINAL-5MM-2
LED1, LED2, LED3: LED1206; LED-1206
P1: ATMEGA328P; DIP28
R1_1: 200; R_0805
R4_1: 51k; R_0805
R5_1: 1k; R_0805
R6_1: 10k; R_0805
R7_1: .1; R_2010
R8, R9, R11: 120; 1206
R8_1, R9_1: 0; R_0603
S1: J_MC32857; J_TOGGLE
X1: HC49S; HC-49

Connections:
BLANK1: H1.12 (BLANK), P1.17 (PB3)
D1: P1.3 (PD1)
EN1: H1.10 (EN), P1.19 (PB5)
EXTMODE1: H1.15 (EXTMODE), P1.16 (PB2)
GND: C1_1.1, C2_1.1, C3_1.1, C4_1.2, C5_1.2, C7_1.2, C8_1.2, C9_1.2, C10_1.1, C11_1.2, C12_1.1, E1.5, H1.5 (GND), H1.6 (GND1), H1.7 (GND2), H1.8 (GND3), H1.18 (GND4), H1.19 (GND5), LED1.C, LED2.C, LED3.C, P1.8 (GND), P1.22 (GND1), R6_1.2, R7_1.2, S1.P$1 (1); also elsewhere on the board
INTERRUPT1_1: E1.2, P1.5 (PD3), R9_1.1
INTERRUPT2_1: E1.1, P1.4 (PD2)
ISENSE1: C9_1.1, H1.17 (SENSE), P1.26 (PC3), R7_1.1
LED1_1: P1.12 (PD6), R8.2
LED2_1: P1.13 (PD7), R9.2
unnamed: LED3.A, R8.1
unnamed: LED2.A, R9.1
unnamed: LED1.A, R11.1
unnamed: C3_1.2, P1.10 (XTAL2), X1.P$1 (1)
unnamed: C2_1.2, P1.9 (XTAL1), X1.P$2 (2)
unnamed: C5_1.1, P1.21 (AREF)
unnamed: P1.1 (PC6), R1_1.1, R11.2, S1.P$2 (2)
unnamed: C6_1.1, H1.1 (CP2)
unnamed: C6_1.2, H1.2 (CP1)
unnamed: H1.4 (ROSC), R4_1.2
unnamed: C12_1.2, H1.24 (CP)
unnamed: C11_1.1, H1.23 (VREG)
unnamed: E1.3, R8_1.1
OUTA1: H1.16 (OUTA), JP6.2
OUTB1: H1.21 (OUTB), JP6.1
PFD1_1: H1.13 (PFD1), P1.14 (PB0)
PFD2_1: H1.11 (PFD2), P1.18 (PB4)
PHASE1: H1.3 (PHASE), P1.23 (PC0)
PULSE1: P1.11 (PD5), R8_1.2, R9_1.2
R1: P1.2 (PD0)
REF1: C8_1.1, H1.14 (REF), R5_1.1, R6_1.1
REF1_1: P1.15 (PB1), R5_1.2
SCL: P1.28 (PC5); also elsewhere on the board
SDA: P1.27 (PC4); also elsewhere on the board
SLEEP1_1: H1.22 (SLEEP), P1.24 (PC1)
V5: C1_1.2, C4_1.1, C7_1.1, E1.4, H1.9 (VDD), P1.7 (VCC), P1.20 (AVCC), R1_1.2, R4_1.1; also elsewhere on the board
VIN: C10_1.2, H1.20 (VBB); also elsewhere on the board

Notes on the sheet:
Connectors
Microcontroller
H-Bridge
Solder Jumpers to Select Encoding Mode

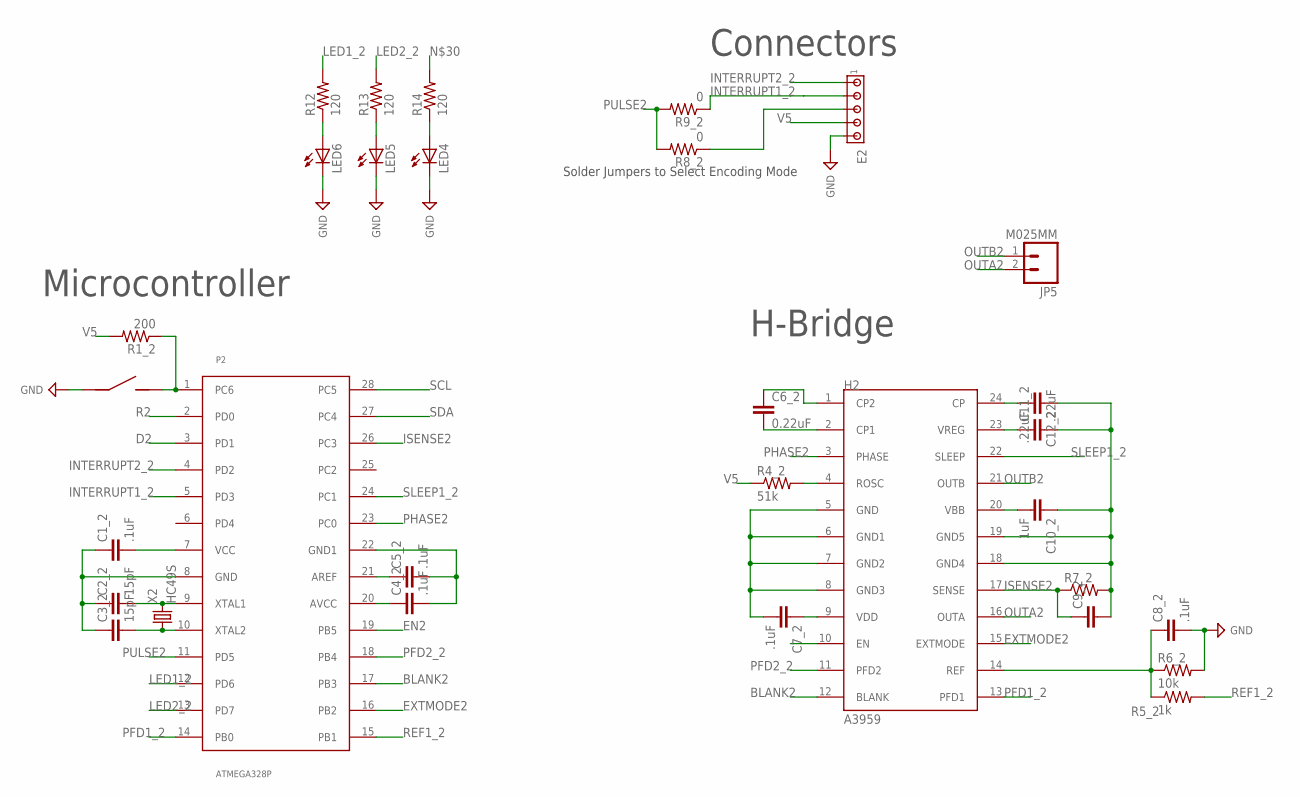
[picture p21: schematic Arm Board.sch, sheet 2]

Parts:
C1_2, C4_2, C5_2, C7_2, C8_2: .1uF; C_0805
C2_2, C3_2: 15pF; C_0805
C6_2: 0.22uF; C_0805
C9_2: C_CAP_0805; C_0805
C10_2: 1uF; C_0805
C11_2, C12_2: .22uF; C_0805
E2: J_MTA5P_100; J_MTA100_5P
H2: A3959; DIP24
JP5: M025MM; SCREWTERMINAL-5MM-2
LED4, LED5, LED6: LED1206; LED-1206
P2: ATMEGA328P; DIP28
R1_2: 200; R_0805
R4_2: 51k; R_0805
R5_2: 1k; R_0805
R6_2: 10k; R_0805
R7_2: R_RES_2010; R_2010
R8_2, R9_2: 0; R_0603
R12, R13, R14: 120; 1206
S2: J_MC32857; J_TOGGLE
X2: HC49S; HC-49

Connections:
BLANK2: H2.12 (BLANK), P2.17 (PB3)
D2: P2.3 (PD1)
EN2: H2.10 (EN), P2.19 (PB5)
EXTMODE2: H2.15 (EXTMODE), P2.16 (PB2)
GND: C1_2.1, C2_2.1, C3_2.1, C4_2.2, C5_2.2, C7_2.2, C8_2.2, C9_2.2, C10_2.1, C11_2.2, C12_2.1, E2.5, H2.5 (GND), H2.6 (GND1), H2.7 (GND2), H2.8 (GND3), H2.18 (GND4), H2.19 (GND5), LED4.C, LED5.C, LED6.C, P2.8 (GND), P2.22 (GND1), R6_2.2, R7_2.2, S2.P$1 (1); also elsewhere on the board
INTERRUPT1_2: E2.2, P2.5 (PD3), R9_2.1
INTERRUPT2_2: E2.1, P2.4 (PD2)
ISENSE2: C9_2.1, H2.17 (SENSE), P2.26 (PC3), R7_2.1
LED1_2: P2.12 (PD6), R12.2
LED2_2: P2.13 (PD7), R13.2
unnamed: LED6.A, R12.1
unnamed: LED5.A, R13.1
unnamed: LED4.A, R14.1
unnamed: C3_2.2, P2.10 (XTAL2), X2.P$1 (1)
unnamed: C2_2.2, P2.9 (XTAL1), X2.P$2 (2)
unnamed: C5_2.1, P2.21 (AREF)
unnamed: P2.1 (PC6), R1_2.1, R14.2, S2.P$2 (2)
unnamed: C6_2.1, H2.1 (CP2)
unnamed: C6_2.2, H2.2 (CP1)
unnamed: H2.4 (ROSC), R4_2.2
unnamed: C12_2.2, H2.24 (CP)
unnamed: C11_2.1, H2.23 (VREG)
unnamed: E2.3, R8_2.1
OUTA2: H2.16 (OUTA), JP5.2
OUTB2: H2.21 (OUTB), JP5.1
PFD1_2: H2.13 (PFD1), P2.14 (PB0)
PFD2_2: H2.11 (PFD2), P2.18 (PB4)
PHASE2: H2.3 (PHASE), P2.23 (PC0)
PULSE2: P2.11 (PD5), R8_2.2, R9_2.2
R2: P2.2 (PD0)
REF1_2: P2.15 (PB1), R5_2.2
REF2: C8_2.1, H2.14 (REF), R5_2.1, R6_2.1
SCL: P2.28 (PC5); also elsewhere on the board
SDA: P2.27 (PC4); also elsewhere on the board
SLEEP1_2: H2.22 (SLEEP), P2.24 (PC1)
V5: C1_2.2, C4_2.1, C7_2.1, E2.4, H2.9 (VDD), P2.7 (VCC), P2.20 (AVCC), R1_2.2, R4_2.1; also elsewhere on the board
VIN: C10_2.2, H2.20 (VBB); also elsewhere on the board

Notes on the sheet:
Connectors
Microcontroller
H-Bridge
Solder Jumpers to Select Encoding Mode

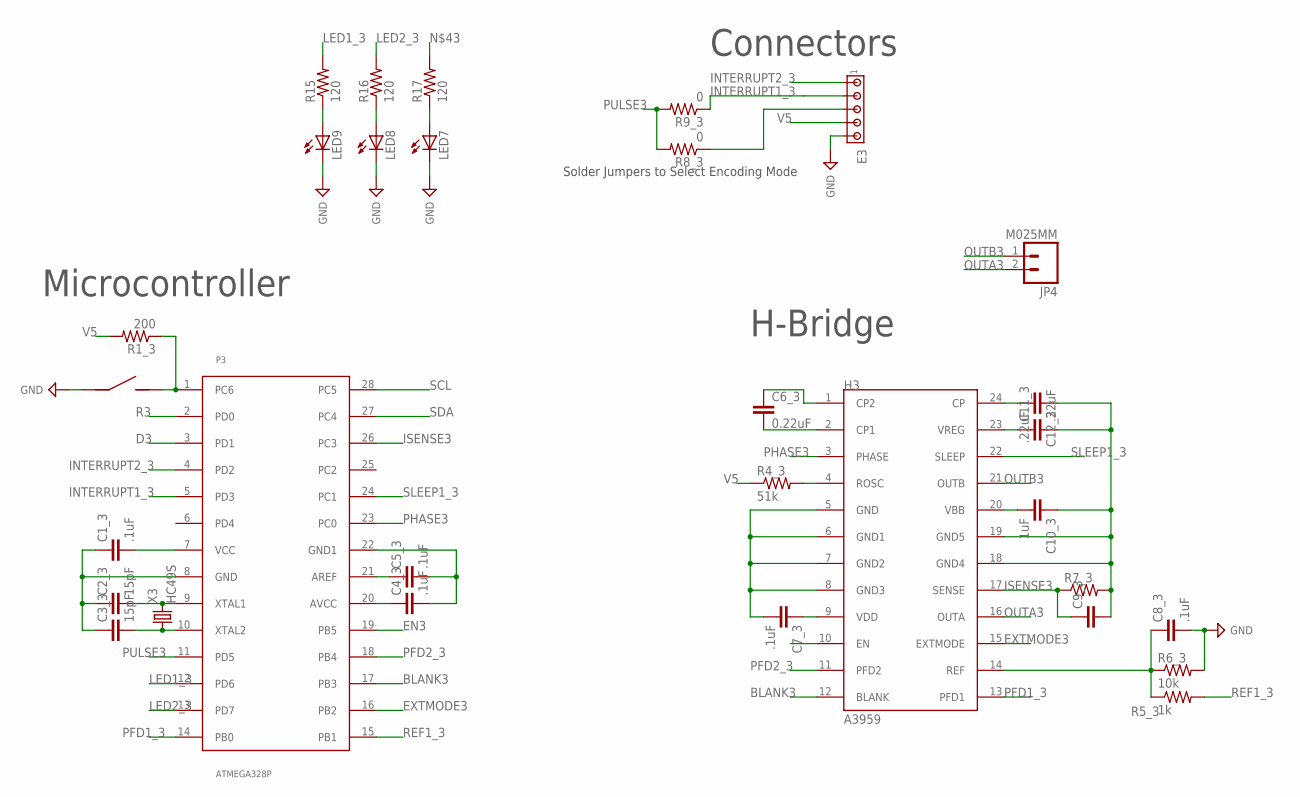
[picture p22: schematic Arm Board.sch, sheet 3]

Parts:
C1_3, C4_3, C5_3, C7_3, C8_3: .1uF; C_0805
C2_3, C3_3: 15pF; C_0805
C6_3: 0.22uF; C_0805
C9_3: C_CAP_0805; C_0805
C10_3: 1uF; C_0805
C11_3, C12_3: .22uF; C_0805
E3: J_MTA5P_100; J_MTA100_5P
H3: A3959; DIP24
JP4: M025MM; SCREWTERMINAL-5MM-2
LED7, LED8, LED9: LED1206; LED-1206
P3: ATMEGA328P; DIP28
R1_3: 200; R_0805
R4_3: 51k; R_0805
R5_3: 1k; R_0805
R6_3: 10k; R_0805
R7_3: R_RES_2010; R_2010
R8_3, R9_3: 0; R_0603
R15, R16, R17: 120; 1206
S3: J_MC32857; J_TOGGLE
X3: HC49S; HC-49

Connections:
BLANK3: H3.12 (BLANK), P3.17 (PB3)
D3: P3.3 (PD1)
EN3: H3.10 (EN), P3.19 (PB5)
EXTMODE3: H3.15 (EXTMODE), P3.16 (PB2)
GND: C1_3.1, C2_3.1, C3_3.1, C4_3.2, C5_3.2, C7_3.2, C8_3.2, C9_3.2, C10_3.1, C11_3.2, C12_3.1, E3.5, H3.5 (GND), H3.6 (GND1), H3.7 (GND2), H3.8 (GND3), H3.18 (GND4), H3.19 (GND5), LED7.C, LED8.C, LED9.C, P3.8 (GND), P3.22 (GND1), R6_3.2, R7_3.2, S3.P$1 (1); also elsewhere on the board
INTERRUPT1_3: E3.2, P3.5 (PD3), R9_3.1
INTERRUPT2_3: E3.1, P3.4 (PD2)
ISENSE3: C9_3.1, H3.17 (SENSE), P3.26 (PC3), R7_3.1
LED1_3: P3.12 (PD6), R15.2
LED2_3: P3.13 (PD7), R16.2
unnamed: LED9.A, R15.1
unnamed: LED8.A, R16.1
unnamed: LED7.A, R17.1
unnamed: C3_3.2, P3.10 (XTAL2), X3.P$1 (1)
unnamed: C2_3.2, P3.9 (XTAL1), X3.P$2 (2)
unnamed: C5_3.1, P3.21 (AREF)
unnamed: P3.1 (PC6), R1_3.1, R17.2, S3.P$2 (2)
unnamed: C6_3.1, H3.1 (CP2)
unnamed: C6_3.2, H3.2 (CP1)
unnamed: H3.4 (ROSC), R4_3.2
unnamed: C12_3.2, H3.24 (CP)
unnamed: C11_3.1, H3.23 (VREG)
unnamed: E3.3, R8_3.1
OUTA3: H3.16 (OUTA), JP4.2
OUTB3: H3.21 (OUTB), JP4.1
PFD1_3: H3.13 (PFD1), P3.14 (PB0)
PFD2_3: H3.11 (PFD2), P3.18 (PB4)
PHASE3: H3.3 (PHASE), P3.23 (PC0)
PULSE3: P3.11 (PD5), R8_3.2, R9_3.2
R3: P3.2 (PD0)
REF1_3: P3.15 (PB1), R5_3.2
REF3: C8_3.1, H3.14 (REF), R5_3.1, R6_3.1
SCL: P3.28 (PC5); also elsewhere on the board
SDA: P3.27 (PC4); also elsewhere on the board
SLEEP1_3: H3.22 (SLEEP), P3.24 (PC1)
V5: C1_3.2, C4_3.1, C7_3.1, E3.4, H3.9 (VDD), P3.7 (VCC), P3.20 (AVCC), R1_3.2, R4_3.1; also elsewhere on the board
VIN: C10_3.2, H3.20 (VBB); also elsewhere on the board

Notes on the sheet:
Connectors
Microcontroller
H-Bridge
Solder Jumpers to Select Encoding Mode

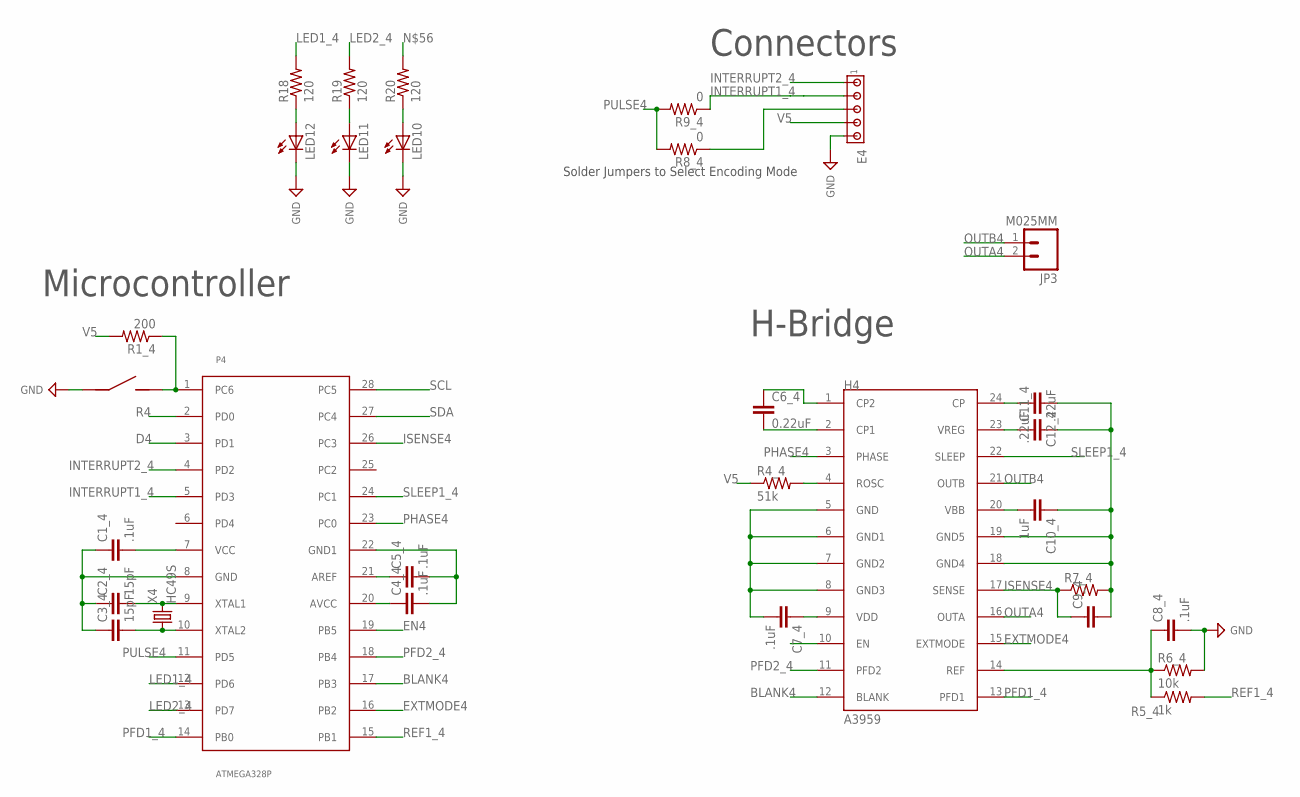
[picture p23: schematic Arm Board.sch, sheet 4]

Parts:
C1_4, C4_4, C5_4, C7_4, C8_4: .1uF; C_0805
C2_4, C3_4: 15pF; C_0805
C6_4: 0.22uF; C_0805
C9_4: C_CAP_0805; C_0805
C10_4: 1uF; C_0805
C11_4, C12_4: .22uF; C_0805
E4: J_MTA5P_100; J_MTA100_5P
H4: A3959; DIP24
JP3: M025MM; SCREWTERMINAL-5MM-2
LED10, LED11, LED12: LED1206; LED-1206
P4: ATMEGA328P; DIP28
R1_4: 200; R_0805
R4_4: 51k; R_0805
R5_4: 1k; R_0805
R6_4: 10k; R_0805
R7_4: R_RES_2010; R_2010
R8_4, R9_4: 0; R_0603
R18, R19, R20: 120; 1206
S4: J_MC32857; J_TOGGLE
X4: HC49S; HC-49

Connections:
BLANK4: H4.12 (BLANK), P4.17 (PB3)
D4: P4.3 (PD1)
EN4: H4.10 (EN), P4.19 (PB5)
EXTMODE4: H4.15 (EXTMODE), P4.16 (PB2)
GND: C1_4.1, C2_4.1, C3_4.1, C4_4.2, C5_4.2, C7_4.2, C8_4.2, C9_4.2, C10_4.1, C11_4.2, C12_4.1, E4.5, H4.5 (GND), H4.6 (GND1), H4.7 (GND2), H4.8 (GND3), H4.18 (GND4), H4.19 (GND5), LED10.C, LED11.C, LED12.C, P4.8 (GND), P4.22 (GND1), R6_4.2, R7_4.2, S4.P$1 (1); also elsewhere on the board
INTERRUPT1_4: E4.2, P4.5 (PD3), R9_4.1
INTERRUPT2_4: E4.1, P4.4 (PD2)
ISENSE4: C9_4.1, H4.17 (SENSE), P4.26 (PC3), R7_4.1
LED1_4: P4.12 (PD6), R18.2
LED2_4: P4.13 (PD7), R19.2
unnamed: LED12.A, R18.1
unnamed: LED11.A, R19.1
unnamed: LED10.A, R20.1
unnamed: C3_4.2, P4.10 (XTAL2), X4.P$1 (1)
unnamed: C2_4.2, P4.9 (XTAL1), X4.P$2 (2)
unnamed: C5_4.1, P4.21 (AREF)
unnamed: P4.1 (PC6), R1_4.1, R20.2, S4.P$2 (2)
unnamed: C6_4.1, H4.1 (CP2)
unnamed: C6_4.2, H4.2 (CP1)
unnamed: H4.4 (ROSC), R4_4.2
unnamed: C12_4.2, H4.24 (CP)
unnamed: C11_4.1, H4.23 (VREG)
unnamed: E4.3, R8_4.1
OUTA4: H4.16 (OUTA), JP3.2
OUTB4: H4.21 (OUTB), JP3.1
PFD1_4: H4.13 (PFD1), P4.14 (PB0)
PFD2_4: H4.11 (PFD2), P4.18 (PB4)
PHASE4: H4.3 (PHASE), P4.23 (PC0)
PULSE4: P4.11 (PD5), R8_4.2, R9_4.2
R4: P4.2 (PD0)
REF1_4: P4.15 (PB1), R5_4.2
REF4: C8_4.1, H4.14 (REF), R5_4.1, R6_4.1
SCL: P4.28 (PC5); also elsewhere on the board
SDA: P4.27 (PC4); also elsewhere on the board
SLEEP1_4: H4.22 (SLEEP), P4.24 (PC1)
V5: C1_4.2, C4_4.1, C7_4.1, E4.4, H4.9 (VDD), P4.7 (VCC), P4.20 (AVCC), R1_4.2, R4_4.1; also elsewhere on the board
VIN: C10_4.2, H4.20 (VBB); also elsewhere on the board

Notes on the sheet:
Connectors
Microcontroller
H-Bridge
Solder Jumpers to Select Encoding Mode

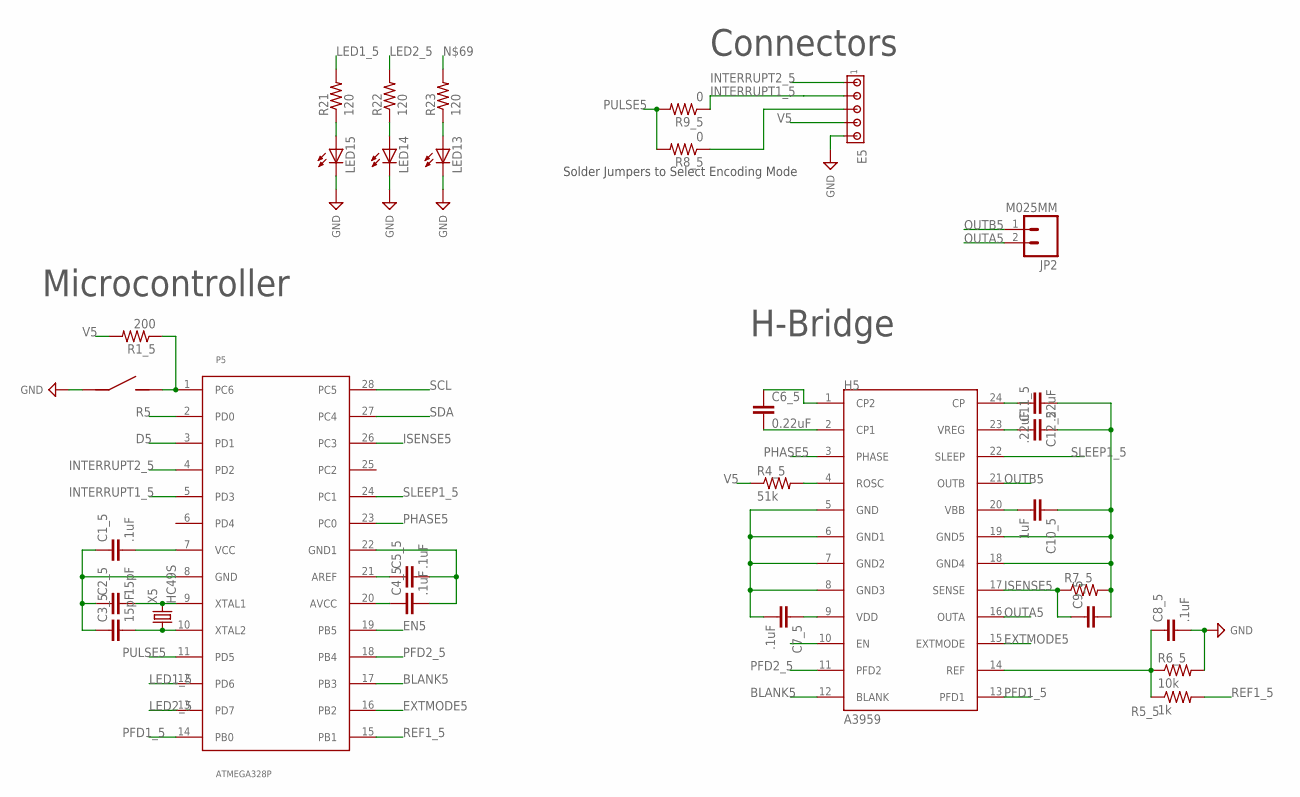
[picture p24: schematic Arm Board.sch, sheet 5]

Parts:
C1_5, C4_5, C5_5, C7_5, C8_5: .1uF; C_0805
C2_5, C3_5: 15pF; C_0805
C6_5: 0.22uF; C_0805
C9_5: C_CAP_0805; C_0805
C10_5: 1uF; C_0805
C11_5, C12_5: .22uF; C_0805
E5: J_MTA5P_100; J_MTA100_5P
H5: A3959; DIP24
JP2: M025MM; SCREWTERMINAL-5MM-2
LED13, LED14, LED15: LED1206; LED-1206
P5: ATMEGA328P; DIP28
R1_5: 200; R_0805
R4_5: 51k; R_0805
R5_5: 1k; R_0805
R6_5: 10k; R_0805
R7_5: R_RES_2010; R_2010
R8_5, R9_5: 0; R_0603
R21, R22, R23: 120; 1206
S5: J_MC32857; J_TOGGLE
X5: HC49S; HC-49

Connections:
BLANK5: H5.12 (BLANK), P5.17 (PB3)
D5: P5.3 (PD1)
EN5: H5.10 (EN), P5.19 (PB5)
EXTMODE5: H5.15 (EXTMODE), P5.16 (PB2)
GND: C1_5.1, C2_5.1, C3_5.1, C4_5.2, C5_5.2, C7_5.2, C8_5.2, C9_5.2, C10_5.1, C11_5.2, C12_5.1, E5.5, H5.5 (GND), H5.6 (GND1), H5.7 (GND2), H5.8 (GND3), H5.18 (GND4), H5.19 (GND5), LED13.C, LED14.C, LED15.C, P5.8 (GND), P5.22 (GND1), R6_5.2, R7_5.2, S5.P$1 (1); also elsewhere on the board
INTERRUPT1_5: E5.2, P5.5 (PD3), R9_5.1
INTERRUPT2_5: E5.1, P5.4 (PD2)
ISENSE5: C9_5.1, H5.17 (SENSE), P5.26 (PC3), R7_5.1
LED1_5: P5.12 (PD6), R21.2
LED2_5: P5.13 (PD7), R22.2
unnamed: LED15.A, R21.1
unnamed: LED14.A, R22.1
unnamed: LED13.A, R23.1
unnamed: C3_5.2, P5.10 (XTAL2), X5.P$1 (1)
unnamed: C2_5.2, P5.9 (XTAL1), X5.P$2 (2)
unnamed: C5_5.1, P5.21 (AREF)
unnamed: P5.1 (PC6), R1_5.1, R23.2, S5.P$2 (2)
unnamed: C6_5.1, H5.1 (CP2)
unnamed: C6_5.2, H5.2 (CP1)
unnamed: H5.4 (ROSC), R4_5.2
unnamed: C12_5.2, H5.24 (CP)
unnamed: C11_5.1, H5.23 (VREG)
unnamed: E5.3, R8_5.1
OUTA5: H5.16 (OUTA), JP2.2
OUTB5: H5.21 (OUTB), JP2.1
PFD1_5: H5.13 (PFD1), P5.14 (PB0)
PFD2_5: H5.11 (PFD2), P5.18 (PB4)
PHASE5: H5.3 (PHASE), P5.23 (PC0)
PULSE5: P5.11 (PD5), R8_5.2, R9_5.2
R5: P5.2 (PD0)
REF1_5: P5.15 (PB1), R5_5.2
REF5: C8_5.1, H5.14 (REF), R5_5.1, R6_5.1
SCL: P5.28 (PC5); also elsewhere on the board
SDA: P5.27 (PC4); also elsewhere on the board
SLEEP1_5: H5.22 (SLEEP), P5.24 (PC1)
V5: C1_5.2, C4_5.1, C7_5.1, E5.4, H5.9 (VDD), P5.7 (VCC), P5.20 (AVCC), R1_5.2, R4_5.1; also elsewhere on the board
VIN: C10_5.2, H5.20 (VBB); also elsewhere on the board

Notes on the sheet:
Connectors
Microcontroller
H-Bridge
Solder Jumpers to Select Encoding Mode


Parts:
C1_6, C4_6, C5_6: .1uF; C_0805
C2_6, C3_6: 15pF; C_0805
J6: J_MC32857; J_TOGGLE
LED16, LED17, LED18: LED1206; LED-1206
O6: M041X04_NO_SILK; 1X04_NO_SILK
P6: ATMEGA328P; DIP28
R1_6: 200; R_0805
R10: 220; AXIAL-0.3EZ
R24, R25, R26: 120; 1206
U$26: MAX485DIL; DIL08
X6: HC49S; HC-49

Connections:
D7: P6.3 (PD1)
D+: O6.3, R10.P$2 (2), U$26.6 (A)
D-: O6.4, R10.P$1 (1), U$26.7 (B)
DIR6: P6.6 (PD4), U$26.2 (RE), U$26.3 (DE)
GND: C1_6.1, C2_6.1, C3_6.1, C4_6.2, C5_6.2, J6.P$1 (1), LED16.C, LED17.C, LED18.C, O6.1, P6.8 (GND), P6.22 (GND1), U$26.5 (GND); also elsewhere on the board
LED1_6: P6.12 (PD6), R24.2
LED2_6: P6.13 (PD7), R25.2
unnamed: LED18.A, R24.1
unnamed: LED17.A, R25.1
unnamed: LED16.A, R26.1
unnamed: C3_6.2, P6.10 (XTAL2), X6.P$1 (1)
unnamed: C2_6.2, P6.9 (XTAL1), X6.P$2 (2)
unnamed: C5_6.1, P6.21 (AREF)
R7: P6.2 (PD0)
S6: J6.P$2 (2), P6.1 (PC6), R1_6.1, R26.2
SCL: P6.28 (PC5); also elsewhere on the board
SD6: P6.5 (PD3), U$26.4 (DI)
SDA: P6.27 (PC4); also elsewhere on the board
SR6: P6.4 (PD2), U$26.1 (RO)
V5: C1_6.2, C4_6.1, P6.7 (VCC), P6.20 (AVCC), R1_6.2, U$26.8 (VCC); also elsewhere on the board
VIN: O6.2; also elsewhere on the board

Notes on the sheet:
Connectors
Microcontroller
RS-485

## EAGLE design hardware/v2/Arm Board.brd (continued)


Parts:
C1_M, C4_M, C5_M: .1uF; C_0805
C2_M, C3_M: 15pF; C_0805
C10: .1uF; CAP-PTH-SMALL-KIT
JP7, JP8: M041X04_NO_SILK; 1X04_NO_SILK
JP9, JP10, JP11, JP12, JP13: M02PTH; 1X02
JP14, JP15: M03PTH; 1X03
LED21: LED1206; LED-1206
MD: J_MTA3P_100; J_MTA100_3P
MP: ATMEGA328P; DIP28
MS, MS1: J_MC32857; J_TOGGLE
MX: HC49S; HC-49
Q1, Q2, Q4: MOSFET-NCHANNELFQP30N06L; TO220V
Q3: Q_LTC490; DIP8
R1, R2: 1.5K Ohm; AXIAL-0.3
R1_M, R1_M1: 200; R_0805
R3, R6, R7: 150; AXIAL-0.3-KIT
R4, R5: 120 Ohm; AXIAL-0.3
R27: 120; 1206
R28, R29, R30, R31, R32: 200; 1/6W-RES
SJ1: SOLDERJUMPERTRACE; SJ_2S-TRACE
U$2: RJ45-8PTH; RJ45-8

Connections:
B1: JP9.2, MP.4 (PD2), R28.2
B2: JP10.2, MP.5 (PD3), R29.2
B3: JP11.2, MP.6 (PD4), R30.2
B4: JP12.2, MP.13 (PD7), R31.2
B5: JP13.2, MP.14 (PB0), R32.2
DM: MD.2, MP.3 (PD1), Q3.3 (D)
GND: C1_M.1, C2_M.1, C3_M.1, C4_M.2, C5_M.2, C10.2, JP14.1, JP15.1, LED21.C, MD.1, MP.8 (GND), MP.22 (GND1), MS.P$1 (1), MS1.P$1 (1), Q1.3 (S), Q2.3 (S), Q3.4 (GND), Q4.3 (S), R3.P$1 (1), R6.P$1 (1), R7.P$1 (1), R28.1, R29.1, R30.1, R31.1, R32.1, SJ1.1; also elsewhere on the board
unnamed: Q3.8 (A), R4.P$1 (1), U$2.3
unnamed: Q3.5 (Y), R5.P$2 (2), U$2.1
unnamed: SJ1.2, U$2.7, U$2.8
unnamed: Q3.6 (Z), R5.P$1 (1), U$2.2
unnamed: Q3.7 (B), R4.P$2 (2), U$2.6
unnamed: LED21.A, R27.1
unnamed: MP.26 (PC3), MS1.P$2 (2), R1_M1.1
unnamed: C3_M.2, MP.10 (XTAL2), MX.P$1 (1)
unnamed: C2_M.2, MP.9 (XTAL1), MX.P$2 (2)
unnamed: C5_M.1, MP.21 (AREF)
unnamed: MP.1 (PC6), MS.P$2 (2), R1_M.1, R27.2
O1: JP7.2, JP8.2, Q1.2 (D)
O2: JP7.3, JP8.3, Q2.2 (D)
O3: JP7.4, JP8.4, Q4.2 (D)
PWM1: JP15.3, MP.11 (PD5)
PWM2: JP14.3, MP.12 (PD6)
RM: MD.3, MP.2 (PD0), Q3.2 (R)
S1: MP.15 (PB1), Q1.1 (G), R3.P$2 (2)
S2: MP.16 (PB2), Q2.1 (G), R6.P$2 (2)
S3: MP.17 (PB3), Q4.1 (G), R7.P$2 (2)
SCL: MP.28 (PC5), R1.P$2 (2); also elsewhere on the board
SDA: MP.27 (PC4), R2.P$2 (2); also elsewhere on the board
V5: C1_M.2, C4_M.1, C10.1, JP9.1, JP10.1, JP11.1, JP12.1, JP13.1, JP14.2, JP15.2, MP.7 (VCC), MP.20 (AVCC), Q3.1 (VCC), R1.P$1 (1), R1_M.2, R1_M1.2, R2.P$1 (1); also elsewhere on the board
VIN: JP7.1, JP8.1; also elsewhere on the board

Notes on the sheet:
Microcontroller


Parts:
CV3, CV4: .1uF; C_0805
JP1: M025MM; SCREWTERMINAL-5MM-2
Q5: LDO; TO-220

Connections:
GND: CV3.2, CV4.2, JP1.2, Q5.2 (GND); also elsewhere on the board
V5: CV4.1, Q5.3 (VOUT); also elsewhere on the board
VIN: CV3.1, JP1.1, Q5.1 (VIN); also elsewhere on the board

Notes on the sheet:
Powersupply


Board: 2 copper layers, 182.9 x 190.5 mm, 219 parts (0 on the bottom side), 195 nets.

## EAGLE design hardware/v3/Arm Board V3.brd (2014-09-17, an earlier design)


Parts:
C13, C14, C15, C17, C18, C19, C20, C21, C22, C23: 0.1uF; 0603-CAP
H1, H2, H3, H4: H_MNTHOLE_#4
IC4, IC5, IC6: 7812TV; TO220V
IC7, IC9: 7812DT; TO252
JP1, JP2, JP3, JP4, JP5, JP6: M025MM; SCREWTERMINAL-5MM-2

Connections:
12V: C19.1, C20.1, C22.1, IC6.3 (VO), IC7.1 (VI), IC9.1 (VI)
+3V3: C23.1, IC9.2 (VO); also elsewhere on the board
+5V: C21.1, IC7.2 (VO); also elsewhere on the board
+12V: C15.1, IC4.3 (VO); also elsewhere on the board
+18V: C14.1, IC5.3 (VO); also elsewhere on the board
A1_1: JP2.1; also elsewhere on the board
A1_2: JP4.1; also elsewhere on the board
A1_3: JP6.2; also elsewhere on the board
A2_1: JP2.2; also elsewhere on the board
A2_2: JP4.2; also elsewhere on the board
A2_3: JP6.1; also elsewhere on the board
B1_1: JP3.1; also elsewhere on the board
B1_2: JP5.1; also elsewhere on the board
B2_1: JP3.2; also elsewhere on the board
B2_2: JP5.2; also elsewhere on the board
GND: C13.2, C14.2, C15.2, C17.2, C18.2, C19.2, C20.2, C21.2, C22.2, C23.2, H1.1, H2.1, H3.1, H4.1, IC4.2 (GND), IC5.2 (GND), IC6.2 (GND), IC7.3 (GND), IC9.3 (GND), JP1.2; also elsewhere on the board
VIN: C13.1, C17.1, C18.1, IC4.1 (VI), IC5.1 (VI), IC6.1 (VI), JP1.1; also elsewhere on the board


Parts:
C1, C4, C7, C8, C11: 5.6nF; 0603-CAP
C2, C5, C9: 10nF; 0603-CAP
C3, C6, C10: 220nF; 0603-CAP
D1, D2, D3, D4, D5, D6: 1N4148; DIODE-1N4148
IC1, IC2, IC3: L6206D; SO24
R1, R3, R5, R6, R8: 100k; 0805
R2, R4, R7: 100; 0805

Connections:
+12V: C3.1, D2.A, IC3.17 (VS_B), IC3.20 (VS_A); also elsewhere on the board
A1_1: IC1.5 (OUT1_A); also elsewhere on the board
A1_2: IC2.5 (OUT1_A); also elsewhere on the board
A1_3: IC3.5 (OUT1_A); also elsewhere on the board
A2_1: IC1.21 (OUT2_A); also elsewhere on the board
A2_2: IC2.21 (OUT2_A); also elsewhere on the board
A2_3: IC3.21 (OUT2_A); also elsewhere on the board
B1_1: IC1.8 (OUT1_B); also elsewhere on the board
B1_2: IC2.8 (OUT1_B); also elsewhere on the board
B2_1: IC1.16 (OUT2_B); also elsewhere on the board
B2_2: IC2.16 (OUT2_B); also elsewhere on the board
EN_A_1: R6.2; also elsewhere on the board
EN_A_2: R3.2; also elsewhere on the board
EN_A_3: R1.2; also elsewhere on the board
EN_B_1: R8.2; also elsewhere on the board
EN_B_2: R5.2; also elsewhere on the board
GND: C1.1, C4.1, C7.2, C8.1, C11.2, IC1.3 (SENSE_A), IC1.6 (GND), IC1.7 (GND), IC1.10 (SENSE_B), IC1.13 (PROGCL_B), IC1.18 (GND), IC1.19 (GND), IC1.24 (PROGCL_A), IC2.3 (SENSE_A), IC2.6 (GND), IC2.7 (GND), IC2.10 (SENSE_B), IC2.13 (PROGCL_B), IC2.18 (GND), IC2.19 (GND), IC2.24 (PROGCL_A), IC3.3 (SENSE_A), IC3.6 (GND), IC3.7 (GND), IC3.10 (SENSE_B), IC3.13 (PROGCL_B), IC3.18 (GND), IC3.19 (GND), IC3.24 (PROGCL_A); also elsewhere on the board
IN1_A_1: IC1.1 (IN1_A); also elsewhere on the board
IN1_A_2: IC2.1 (IN1_A); also elsewhere on the board
IN1_A_3: IC3.1 (IN1_A); also elsewhere on the board
IN1_B_1: IC1.11 (IN1_B); also elsewhere on the board
IN1_B_2: IC2.11 (IN1_B); also elsewhere on the board
IN2_A_1: IC1.2 (IN2_A); also elsewhere on the board
IN2_A_2: IC2.2 (IN2_A); also elsewhere on the board
IN2_A_3: IC3.2 (IN2_A); also elsewhere on the board
IN2_B_1: IC1.12 (IN2_B); also elsewhere on the board
IN2_B_2: IC2.12 (IN2_B); also elsewhere on the board
unnamed: D3.A, D4.C, R4.2
unnamed: D5.A, D6.C, R7.2
unnamed: C5.2, R4.1
unnamed: C9.1, IC1.22 (VCP)
unnamed: C9.2, R7.1
unnamed: C5.1, IC2.22 (VCP)
unnamed: D1.A, D2.C, R2.2
unnamed: C2.2, R2.1
unnamed: C2.1, IC3.22 (VCP)
OCD_A_1: C8.2, IC1.4 (OCD_A), IC1.23 (EN_A), R6.1
OCD_A_2: C4.2, IC2.4 (OCD_A), IC2.23 (EN_A), R3.1
OCD_A_3: C1.2, IC3.4 (OCD_A), IC3.23 (EN_A), R1.1
OCD_B_1: C11.1, IC1.9 (OCD_B), IC1.14 (EN_B), R8.1
OCD_B_2: C7.1, IC2.9 (OCD_B), IC2.14 (EN_B), R5.1
VBOOT_1: C10.2, D5.C, IC1.15 (VBOOT)
VBOOT_2: C6.2, D3.C, IC2.15 (VBOOT)
VBOOT_3: C3.2, D1.C, IC3.15 (VBOOT)
VIN: C6.1, C10.1, D4.A, D6.A, IC1.17 (VS_B), IC1.20 (VS_A), IC2.17 (VS_B), IC2.20 (VS_A); also elsewhere on the board


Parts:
CN1: 1X4-BIG; 1X04-BIG
R9: 220; 0603-RES
U1: MAX3468CPA; DIL08

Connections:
+3V3: U1.8 (VCC); also elsewhere on the board
+18V: CN1.2; also elsewhere on the board
DD+: CN1.3, R9.2, U1.7 (B)
DD-: CN1.4, R9.1, U1.6 (A)
EN485: U1.2 (RE/), U1.3 (DE); also elsewhere on the board
GND: CN1.1, U1.5 (GND); also elsewhere on the board
RXD2: U1.1 (RO); also elsewhere on the board
TXD2: U1.4 (DI); also elsewhere on the board


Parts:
C12: .1uF; 0603-CAP
JP7: M03PTH; 1X03
JP8, JP9: M04PTH; 1X04
Q3: Q_LTC490; DIP8
R10, R11: 120 Ohm; 0603-RES
U$1: STELLARIS-LAUNCHPADSTELLARIS-LAUNCHPAD-XL; LAUNCHPAD-XL
U$3: RJ45-8PTH; RJ45-8

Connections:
+3V3: C12.1, Q3.1 (VCC), U$1.3.3V; also elsewhere on the board
+5V: JP8.2, JP9.2, U$1.VBUS; also elsewhere on the board
A0: JP8.3, U$1.PE3
A7: JP8.4, U$1.PD0
A10: JP9.3, U$1.PB4
A11: JP9.4, U$1.PB5
EN485: U$1.PB3; also elsewhere on the board
EN_A_1: U$1.PE1; also elsewhere on the board
EN_A_2: U$1.PB7; also elsewhere on the board
EN_A_3: U$1.PB6; also elsewhere on the board
EN_B_1: U$1.PE2; also elsewhere on the board
EN_B_2: U$1.PB2; also elsewhere on the board
GND: C12.2, JP7.3, JP8.1, JP9.1, Q3.4 (GND), U$1.GND1, U$1.GND2, U$3.7, U$3.8; also elsewhere on the board
IN1_A_1: U$1.PD1; also elsewhere on the board
IN1_A_2: U$1.PE0; also elsewhere on the board
IN1_A_3: U$1.PA3; also elsewhere on the board
IN1_B_1: U$1.PD2; also elsewhere on the board
IN1_B_2: U$1.PF2; also elsewhere on the board
IN2_A_1: U$1.PA2; also elsewhere on the board
IN2_A_2: U$1.PF0; also elsewhere on the board
IN2_A_3: U$1.PA4; also elsewhere on the board
IN2_B_1: U$1.PD3; also elsewhere on the board
IN2_B_2: U$1.PF3; also elsewhere on the board
unnamed: Q3.6 (Z), R11.1, U$3.2
unnamed: Q3.7 (B), R10.2, U$3.6
unnamed: Q3.8 (A), R10.1, U$3.3
unnamed: Q3.5 (Y), R11.2, U$3.1
RESET: U$1.RST
RXD1: Q3.2 (R), U$1.PC6
RXD2: U$1.PC4; also elsewhere on the board
RXD3: U$1.PD6; also elsewhere on the board
RXD5: JP7.2, U$1.PE4
TXD1: Q3.3 (D), U$1.PC7
TXD2: U$1.PC5; also elsewhere on the board
TXD3: U$1.PD7; also elsewhere on the board
TXD5: JP7.1, U$1.PE5
XRESET: U$1.PF4; also elsewhere on the board

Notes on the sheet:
A0 A7 A10 A11


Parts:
C16: 0.1uF; 0603-CAP
C24: .1uF; 0603-CAP
LED1, LED2: Red; LED-0603
LED3, LED4, LED5: Green; LED-0603
Q1: Q_LTC490; DIP8
R12, R13, R14, R15, R16: 1k; 0603-RES
R17, R18: 120 Ohm; 0603-RES
SJ2: SOLDERJUMPERTRACE; SJ_2S-TRACE
U2: XBEE-1B3; XBEE-SMD
U$2: RJ45-8PTH; RJ45-8

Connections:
+3V3: C24.1, Q1.1 (VCC), R12.2, R13.1, R14.1, U2.1 (VDD); also elsewhere on the board
CTS: U2.12 (CTS)
DIO0: U2.20 (DIO0)
DIO1: U2.19 (DIO1)
DIO2: U2.18 (DIO2)
DIO3: SJ2.2, U2.17 (DIO3)
DIO4: U2.11 (DIO4)
DIO5: R16.2, U2.15 (DIO5)
DIO9: U2.13 (DIO9)
DIO11: U2.7 (DIO11)
DIO12: U2.4 (DIO12)
DTR: U2.9 (DTR)
GND: C24.2, LED1.C, LED4.C, LED5.C, Q1.4 (GND), U2.10 (GND), U$2.7, U$2.8; also elsewhere on the board
unnamed: LED2.A, R13.2
unnamed: LED3.A, R14.2
unnamed: LED4.A, R15.1
unnamed: C16.2, SJ2.1
unnamed: Q1.5 (Y), R18.2, U$2.1
unnamed: Q1.6 (Z), R18.1, U$2.2
unnamed: Q1.7 (B), R17.2, U$2.6
unnamed: Q1.8 (A), R17.1, U$2.3
unnamed: LED1.A, R12.1
unnamed: LED5.A, R16.1
RES1: U2.8 (RES)
RES2: U2.14 (RES)
RSSI: R15.2, U2.6 (RSSI)
RTS: U2.16 (RTS)
RXD3: LED2.C, Q1.2 (R), U2.2 (DOUT); also elsewhere on the board
TXD3: LED3.C, Q1.3 (D), U2.3 (DIN); also elsewhere on the board
XRESET: C16.1, U2.5 (RESET); also elsewhere on the board



Board: 2 copper layers, 165.1 x 76.2 mm, 83 parts (3 on the bottom side), 82 nets.

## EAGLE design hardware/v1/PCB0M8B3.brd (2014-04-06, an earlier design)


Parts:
C1: 330uF; C_8MM
C3: 15pF; C_0805
C4, C5, C6, C7, C14, C15: C_CAP_0805; C_0805
H1, H2: H_MNTHOLE_#4
J1, J2: J_1546074-2282834-2; J_2.54MM
J4: J_MC32857; J_TOGGLE
J5: J_MTA3P_100; J_MTA100_3P
Q3: ATMEGA328P; DIP28
Q4: LDO; TO-220
Q5: LM35; TO-92-3
R1: 200; R_0805
R10, R11: R_RES_0805; R_0805
X1: HC49S; HC-49

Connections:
D: J5.2, Q3.3 (PD1)
GND: C1.-, C3.1, C4.1, C5.1, C6.2, C7.2, C14.2, C15.2, J1.P$2, J4.P$1 (1), J5.1, Q3.8 (GND), Q3.22 (GND1), Q4.2 (GND), Q5.1 (GND), R11.2; also elsewhere on the board
unnamed: C4.2, Q3.10 (XTAL2), X1.P$1 (1)
unnamed: C3.2, Q3.9 (XTAL1), X1.P$2 (2)
unnamed: Q3.27 (PC4), Q5.2 (OUT)
unnamed: Q3.28 (PC5), R10.2, R11.1
unnamed: C6.1, Q3.21 (AREF)
unnamed: J4.P$2 (2), Q3.1 (PC6), R1.1
OUTA: J2.P$2
OUTB: J2.P$1; also elsewhere on the board
R: J5.3, Q3.2 (PD0)
V5: C5.2, C7.1, C15.1, Q3.7 (VCC), Q3.20 (AVCC), Q4.3 (VOUT), Q5.3 (VIN), R1.2; also elsewhere on the board
VIN: C1.+, C14.1, J1.P$1, Q4.1 (VIN), R10.1; also elsewhere on the board

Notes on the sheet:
Powersupply
Connectors
Microcontroller


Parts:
C16, C23: 0.22uF; C_0805
C17, C18, C19, C20, C21, C24, C25, C26, C27, C28: C_CAP_0805; C_0805
C22, C29: 0.1uF; C_0805
Q2, Q6: A3959; DIP24
R6, R16: R_RES_2010; R_2010
R12, R17: 51k; R_0805
R13, R18: R_1/4WL
R14, R19: 10k; R_0805
R15, R20: 1k; R_0805

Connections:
GND: C17.2, C18.2, C19.1, C20.1, C21.2, C22.2, C24.2, C25.2, C26.1, C29.2, Q2.5 (GND), Q2.6 (GND1), Q2.7 (GND2), Q2.8 (GND3), Q2.18 (GND4), Q2.19 (GND5), Q6.5 (GND), Q6.6 (GND1), Q6.7 (GND2), Q6.8 (GND3), Q6.18 (GND4), Q6.19 (GND5), R6.2, R14.2, R16.2, R19.2; also elsewhere on the board
ISENSE: C17.1, C24.1, Q2.17 (SENSE), Q6.17 (SENSE), R6.1, R16.1
unnamed: C16.1, Q2.1 (CP2)
unnamed: C16.2, Q2.2 (CP1)
unnamed: Q2.4 (ROSC), R12.2
unnamed: C20.2, Q2.24 (CP)
unnamed: C21.1, Q2.23 (VREG)
unnamed: Q2.22 (SLEEP), R13.2
unnamed: C23.1, Q6.1 (CP2)
unnamed: C23.2, Q6.2 (CP1)
unnamed: Q6.4 (ROSC), R17.2
unnamed: C27.2, Q6.24 (CP)
unnamed: C28.1, Q6.23 (VREG)
unnamed: Q6.22 (SLEEP), R18.2
unnamed: C27.1, C28.2
OUTB: Q6.21 (OUTB); also elsewhere on the board
REF2: C22.1, Q2.14 (REF), R14.1, R15.1
REF3: C29.1, Q6.14 (REF), R19.1, R20.1
V5: C18.1, C25.1, Q2.9 (VDD), Q6.9 (VDD), R12.1, R17.1; also elsewhere on the board
VIN: C19.2, C26.2, Q2.20 (VBB), Q6.20 (VBB); also elsewhere on the board


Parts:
C9: C_CAP_1206; C_1206
C10, C11, C12, C13, C30: C_CAP_0805; C_0805
Q8, Q9: Q_LFLS7366R-S; SOIC14
X2, X3: X_HC49SCRYSTAL; HC-49

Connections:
GND: C9.2, C10.2, C11.1, C12.1, C13.1, C30.1, Q8.3 (VSS), Q9.3 (VSS); also elsewhere on the board
unnamed: C9.1, Q8.14 (VDD)
unnamed: C10.1, Q9.14 (VDD)
unnamed: C12.2, Q8.2 (FCKI), X3.P$1 (1)
unnamed: C11.2, Q8.1 (FCKO), X3.P$2 (2)
unnamed: C13.2, Q9.1 (FCKO), X2.P$2 (2)
unnamed: C30.2, Q9.2 (FCKI), X2.P$1 (1)


Board: 2 copper layers, 86.4 x 63.5 mm, 57 parts (0 on the bottom side), 34 nets.

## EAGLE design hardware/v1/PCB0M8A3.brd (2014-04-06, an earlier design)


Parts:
C1: 330uF; C_8MM
C2: 0.1uF; C_0805
C3: 15pF; C_0805
C4, C5, C6, C7, C9, C10, C11, C12, C13, C14, C15: C_CAP_0805; C_0805
C8: 0.22uF; C_0805
H1, H2: H_MNTHOLE_#4
J1, J2: J_1546074-2282834-2; J_2.54MM
J3: J_MTA5P_100; J_MTA100_5P
J4: J_MC32857; J_TOGGLE
J5: J_MTA3P_100; J_MTA100_3P
Q1: A3959; DIP24
Q3: ATMEGA328P; DIP28
Q4: LDO; TO-220
Q5: LM35; TO-92-3
R1: 200; R_0805
R2: R_RES_2010; R_2010
R3: 51k; R_0805
R4, R5: R_RES_0603; R_0603
R7: R_1/4WL
R8: 10k; R_0805
R9: 1k; R_0805
R10, R11: R_RES_0805; R_0805
X1: HC49S; HC-49

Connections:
BLANK: Q1.12 (BLANK), Q3.17 (PB3)
D: J5.2, Q3.3 (PD1)
EN: Q1.10 (EN), Q3.19 (PB5)
EXTMODE: Q1.15 (EXTMODE), Q3.16 (PB2)
GND: C1.-, C2.2, C3.1, C4.1, C5.1, C6.2, C7.2, C9.2, C10.2, C11.1, C12.1, C13.2, C14.2, C15.2, J1.P$2, J3.5, J4.P$1 (1), J5.1, Q1.5 (GND), Q1.6 (GND1), Q1.7 (GND2), Q1.8 (GND3), Q1.18 (GND4), Q1.19 (GND5), Q3.8 (GND), Q3.22 (GND1), Q4.2 (GND), Q5.1 (GND), R2.2, R8.2, R11.2
INTERRUPT1: J3.2, Q3.5 (PD3), R4.1
INTERRUPT2: J3.1, Q3.4 (PD2)
ISENSE: C9.1, Q1.17 (SENSE), Q3.26 (PC3), R2.1
unnamed: C4.2, Q3.10 (XTAL2), X1.P$1 (1)
unnamed: C3.2, Q3.9 (XTAL1), X1.P$2 (2)
unnamed: Q1.22 (SLEEP), R7.2
unnamed: Q3.27 (PC4), Q5.2 (OUT)
unnamed: Q3.28 (PC5), R10.2, R11.1
unnamed: C6.1, Q3.21 (AREF)
unnamed: J3.3, R5.1
unnamed: J4.P$2 (2), Q3.1 (PC6), R1.1
unnamed: C8.1, Q1.1 (CP2)
unnamed: C8.2, Q1.2 (CP1)
unnamed: Q1.4 (ROSC), R3.2
unnamed: C12.2, Q1.24 (CP)
unnamed: C13.1, Q1.23 (VREG)
OUTA: J2.P$2, Q1.16 (OUTA)
OUTB: J2.P$1, Q1.21 (OUTB)
PFD1: Q1.13 (PFD1), Q3.14 (PB0)
PFD2: Q1.11 (PFD2), Q3.18 (PB4)
PHASE: Q1.3 (PHASE), Q3.23 (PC0)
PULSE: Q3.11 (PD5), R4.2, R5.2
R: J5.3, Q3.2 (PD0)
REF: C2.1, Q1.14 (REF), R8.1, R9.1
REF1: Q3.15 (PB1), R9.2
SLEEP1: Q3.24 (PC1), R7.1
V5: C5.2, C7.1, C10.1, C15.1, J3.4, Q1.9 (VDD), Q3.7 (VCC), Q3.20 (AVCC), Q4.3 (VOUT), Q5.3 (VIN), R1.2, R3.1
VIN: C1.+, C11.2, C14.1, J1.P$1, Q1.20 (VBB), Q4.1 (VIN), R10.1

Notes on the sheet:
Powersupply
Connectors
Microcontroller
H-Bridge
Solder Jumpers to Select Encoding Mode


Board: 2 copper layers, 58.4 x 48.3 mm, 37 parts (0 on the bottom side), 33 nets.

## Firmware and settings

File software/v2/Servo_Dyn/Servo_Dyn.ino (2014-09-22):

#include <SoftwareSerial.h>

#define HOME_ENCODER : 0x200
#define MAX_ENCODER : 0x3FF
#define RAD_PER_ENC : math.radians(300.0)
#define MAX_AND : math.radians(148)
#define MIN_ANG : math.radians(-148)
#define MAX_SPEED : math.radians(100)

byte instruction[10];
byte inst5[5];
byte inst6[6];
byte inst7[7];
byte inst8[8];
byte inst9[9];
byte inst10[10];
bool FLIPPED = false;

SoftwareSerial mySerial(2, 3); // RX, TX
int EN=4;

void startBits()
{
  instruction[0] = 0xFF;
  instruction[1] = 0xFF;
  instruction[2] = 0x01;
}

void init_cont_turn()
{
  Serial.println("init");
  startBits();
  instruction[3] = 0x04;
  instruction[4] = 0x04;
  instruction[5] = 0x08;
  instruction[6] = 0x00;
  formMsg();
}

void kill_cont_turn()
{
  Serial.println("kill");
  startBits();
  instruction[3] = 0x04;
  instruction[4] = 0x04;
  instruction[5] = 0x08;
  instruction[6] = 0x03;
  formMsg();
}

/*
bool is_moving()
{
  data = read_address(0x2E, 1);
  return(data[0] != 0)
}

float read_voltage()
{
  data = read_address(0x2A, 1);
  return(data[0]/10);
} 
*/
void read_temperature()
{
  int numBytesAvail;
  byte array1[] = {255, 255, 1, 4, 2, 43, 1, 204};
  
  digitalWrite(EN,HIGH);
  mySerial.write(array1, sizeof(array1));
  digitalWrite(EN,LOW);
  delay(100);
  numBytesAvail = mySerial.available();   // get number of bytes in response message 
  for (int i=0; i<numBytesAvail; i++)
    Serial.print(mySerial.read(), HEX);      // print each one as hex number on console
  //data = read_address(0x2B, 1);
}
/*
float read_load()
{
  data = read_address(0x28, 2)
  load = (data[0] + ((data[1] >> 6) * 256));
}

float read_encoder()
{
  data = read_address(0x24, 2);
  load = data[0] + data[1]*256;
  if(data[1] >> 2 & 1 == 0)
    return (-1*load);
  else
    return load;
}

float read_angle()
{
  ang = (read_encoder() - (HOME_ENCODER*RAD_PER_ENC))
  if(FLIPPED)
    ang = ang*-1;
  return ang;
}

void move_angle(ang, angvel = None, blocking = true)
{
  if(angvel == None)
    angvel = MAX_SPEED;
   
  set_angvel(angvel);
 
  if(FLIPPED)
    ang = ang*-1;
   
  enc_tics = int(round(ang/RAD_PER_NENC));
  enc_tics += HOME_ENCODER;
 
  move_to_encoder(enc_tics);
 
  if(blocking == true)
  {
    while(is_moving())
      continue;
  }
}

void move_to_encoder(n)
{
  n = min(max(n,0), MAX_ENCODER);
  hi = n/256;
  lo = n%256;
  write_address(0x1E, [lo,hi]);
}

void enable_torque()
{
  write_address(0x18, [1]);
}

void disable_torque()
{
  write_address(0x18, [0]);
}

void set_angvel(float angvel)
{
  float rpm= angvel / (2 * 3.1415926535897) * 60; 
  int angvel_enc = rpm/0.11;
  if (angvel_enc<0)
  {
    byte hi = abs(angvel_enc) / 256 + 4;
    byte lo = abs(angvel_enc) % 256;
  }
  else
  {
    byte hi = angvel_enc/256;
    byte lo = angvel_enc % 256;
  }
  
  startBits();
  instruction[4] = 0x05;
  instruction[5] = 0x03;
  instruction[6] = 0x08;
  instruction[7] = 0x00;
  formMsg();
}
*/

void send_serial(byte msg[])
{
  int numBytesAvail;
  digitalWrite(EN,HIGH);
  mySerial.write(msg, sizeof(msg));
  digitalWrite(EN,LOW);
  delay(100);  
  numBytesAvail = mySerial.available();   // get number of bytes in response message 
  for (int i=0; i<numBytesAvail; i++)
    Serial.print(mySerial.read(), HEX);      // print each one as hex number on console
}

int formMsg()
{

}

void setup()  
{
  Serial.begin(9600);
  mySerial.begin(57600);     // set the data rate for the SoftwareSerial port
  pinMode(EN,OUTPUT);
}

void loop()
{
  read_temperature();
}

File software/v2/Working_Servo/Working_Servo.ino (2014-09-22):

#include <SoftwareSerial.h>
SoftwareSerial mySerial(2, 3); // RX, TX

int EN=4;

byte array1[] = {255, 255, 1, 4, 2, 3, 1, 244};
byte array2[] = {255, 255, 1, 4, 2, 5, 1, 242};
byte array3[] = {255, 255, 1, 5, 3, 32, 75, 0, 139};
byte array4[] = {255, 255, 1, 5, 3, 30, 17, 0, 199};

byte array11[] = {255, 255, 1, 4, 2, 3, 1, 244};
byte array12[] = {255, 255, 1, 4, 2, 5, 1, 242};
byte array13[] = {255, 255, 1, 5, 3, 32, 75, 0, 139};
byte array14[] = {255, 255, 1, 5, 3, 30, 239, 3, 230};

void setup()  
{
  Serial.begin(9600);
  mySerial.begin(57600);     // set the data rate for the SoftwareSerial port
  pinMode(EN,OUTPUT);
}

void loop() // run over and over
{
  int numBytesAvail;
  
  digitalWrite(EN,HIGH);
  mySerial.write(array1, sizeof(array1));
  digitalWrite(EN,LOW);
  delay(100);
  numBytesAvail = mySerial.available();   // get number of bytes in response message 
  for (int i=0; i<numBytesAvail; i++)
    Serial.print(mySerial.read(), HEX);      // print each one as hex number on console
    
  digitalWrite(EN,HIGH);
  mySerial.write(array2, sizeof(array2));
  
  digitalWrite(EN,LOW);
  delay(100);
  numBytesAvail = mySerial.available();   // get number of bytes in response message 
  for (int i=0; i<numBytesAvail; i++)
    Serial.print(mySerial.read(), HEX);      // print each one as hex number on console
    
  digitalWrite(EN,HIGH);
  mySerial.write(array3, sizeof(array3));
  
  digitalWrite(EN,LOW);
  delay(100);
  numBytesAvail = mySerial.available();   // get number of bytes in response message 
  for (int i=0; i<numBytesAvail; i++)
    Serial.print(mySerial.read(), HEX);      // print each one as hex number on console
    
  digitalWrite(EN,HIGH);
  mySerial.write(array4, sizeof(array4));
  
  digitalWrite(EN,LOW);
  delay(100);
  numBytesAvail = mySerial.available();   // get number of bytes in response message 
  for (int i=0; i<numBytesAvail; i++)
    Serial.print(mySerial.read(), HEX);      // print each one as hex number on console
    
    
  delay(1000);
  
  digitalWrite(EN,HIGH);
  mySerial.write(array11, sizeof(array11));
  
  digitalWrite(EN,LOW);
  delay(100);
  numBytesAvail = mySerial.available();   // get number of bytes in response message 
  for (int i=0; i<numBytesAvail; i++)
    Serial.print(mySerial.read(), HEX);      // print each one as hex number on console
    
  digitalWrite(EN,HIGH);
  mySerial.write(array12, sizeof(array12));
  
  digitalWrite(EN,LOW);
  delay(100);
  numBytesAvail = mySerial.available();   // get number of bytes in response message 
  for (int i=0; i<numBytesAvail; i++)
    Serial.print(mySerial.read(), HEX);      // print each one as hex number on console
    
  digitalWrite(EN,HIGH);
  mySerial.write(array13, sizeof(array13));
  
  digitalWrite(EN,LOW);
  delay(100);
  numBytesAvail = mySerial.available();   // get number of bytes in response message 
  for (int i=0; i<numBytesAvail; i++)
    Serial.print(mySerial.read(), HEX);      // print each one as hex number on console
    
  digitalWrite(EN,HIGH);
  mySerial.write(array14, sizeof(array14));
  
  digitalWrite(EN,LOW);
  delay(100);
  numBytesAvail = mySerial.available();   // get number of bytes in response message 
  for (int i=0; i<numBytesAvail; i++)
    Serial.print(mySerial.read(), HEX);      // print each one as hex number on console
  
  delay(1000);

}

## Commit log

2014-04-06 Added gitignore and hardware files
    [PCB0M8A3.brd, PCB0M8A3.sch, PCB0M8B1.brd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]
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2014-04-28 Conglomerated all arm hardware into single board
    [All.brd, All.sch]
2014-04-29 Updated board. Updated master to control software to use software UARTs to communicate with slaves
    [All.brd, All.sch, Arm Board.brd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]
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2014-05-03 More initialization code for struct serialization. Replace Arduino IDE Software Serial libraries with the included ones
2014-05-03 Stupid file structure changes to fix issues with Arduino IDE
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2014-05-18 Reorganized arm hardware file structure to reflect versioning
    [All.brd, All.sch, Arm Board.brd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]
2014-05-18 A few more hardware file restructuring for organizational purposes. Modified ArmMaster struct to use unint8_t type to be more explicit
    [All.brd, All.sch, Arm Board.brd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]
2014-05-24 Adding the files eric gave me
    [Arm Board.brd, Arm Board.sch]
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2014-09-06 Created v3 Folders
    Created v3 folders and added current v3 schematic and board design.
    [Arm Board V3.brd, Arm Board V3.sch]
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2014-09-07 stuff
    Expanded the board
    Binded EA pin to PWMs
    [Arm Board V3.brd, Arm Board V3.sch]
2014-09-07 Connected motor controllers and Dynamixel
    Bunch of stuff in the schematic
    [Arm Board V3.brd, Arm Board V3.sch]
2014-09-07 Added Xbee connections to schematic
    [Arm Board V3.brd, Arm Board V3.sch]
2014-09-08 Removed old board file and created a new one
    Removed the old board file since there were problems with it from
    copying in the Due. This will also allow us to lay it out logically
    with all of the parts on the board.
    [Arm Board V3.brd, Arm Board V3.sch]
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2014-09-08 Added Launchpad to Board
    This included adding it to the schematic, widening the board, and
    placing components.
    [Arm Board V3.brd, Arm Board V3.sch]
2014-09-08 Moved old version of board to a folder
    [Arm Board V3 Arduino.sch]
2014-09-08 Started routing and added RJ-45
    [Arm Board V3.brd, Arm Board V3.sch]
2014-09-09 Started assigning serial pins and routing
    Also added picture of TI Launchpad pinout (It will be fun when it comes
    time to add encoders)
    [Arm Board V3.brd, Arm Board V3.sch]
2014-09-09 Added enable pins to schematic and routed
    [Arm Board V3.brd, Arm Board V3.sch]
2014-09-09 Did some more routing on the board
    [Arm Board V3.brd, Arm Board V3.sch]
2014-09-09 Moved a few things around
    [Arm Board V3.brd]
2014-09-10 Redid Xbee as well as moved things around
    [Arm Board V3.brd, Arm Board V3.sch]
2014-09-10 Changed some stuff on launchpad
    [Arm Board V3.brd, Arm Board V3.sch]
2014-09-11 Routed stuffs and stuffs and moved stuff and stuffs
    [Arm Board V3.brd, Arm Board V3.sch]
2014-09-12 Routing and Voltage Regulators (See Notes)
    Started to route all of the pins towards the processor. They need to be
    reordered/reassigned since they do not make routing sense. Added the
    +12V and +18V regulators and hooked them up. The +3V3 and +5V still
    need to be picked and placed.
    [Arm Board V3.brd, Arm Board V3.sch]
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2014-09-12 5v and 3v3 power rails
    Added a second 12v regulator to drive the 5v and 3v3 regulator
    [Arm Board V3.brd, Arm Board V3.sch]
2014-09-13 Finished Routing Data Lines
    [Arm Board V3.brd, Arm Board V3.sch]
2014-09-13 Did some clean up
    [Arm Board V3.brd, Sample End Effector.brd, Sample End Effector.sch]
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2014-09-15 Finished assigning values and fixing errors
    [Arm Board V3.brd, Arm Board V3.sch]
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2014-09-16 Added headers for serial in and 2 encoders
    [Arm Board V3.brd, Arm Board V3.sch]
2014-09-16 Cleaned up and made sure it complied with 4pcb DRU
    [Arm Board V3.brd]
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2014-09-17 Finished cleanup
    Now Alec needs to verify it all
    [Arm Board V3.brd]
2014-09-17 This finishes the board design and closes #3
    [Arm Board V3.brd]
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2014-10-27 Continued work on V4
    Started to route power and fixed inconsistency
    [Arm Board V4.brd, Arm Board V4.sch]
2014-10-27 Router power and data lines and assigned pins
    Started to route more of the data lines to where they will go. As well
    as working on assigning pins to components.
    [Arm Board V4.brd, Arm Board V4.sch]
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2014-10-28 Added a few things and cleaned up some stuff
    Added a few things from last night but mostly cleaning up traces and
    adding parts to it. Commit message last night was by Seto so ignore the
    message.
    [Arm Board V4.brd, Arm Board V4.sch]
2014-11-04 A lot of updates getting close to a final board
    Did a lot of changes that got the board closer to the final version.
    Skipped a lot of commits because who cares and github was not getting
    along with me.
    [Arm Board V4.brd, Arm Board V4.sch]
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2014-11-04 Pour and Spacing changes
    Worked on spacing the pours and power connectors so they made sense for
    pluggable screw terminals.
    [Arm Board V4.brd]
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2014-11-04 Added a few capacitors
    Added capacitors on voltage supplies and regulator.
    [Arm Board V4.brd, Arm Board V4.sch]
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2014-11-07 Just a few things with rearranging components
    Moved some power connectors and a few pours
    [Arm Board V4.brd, Arm Board V4.sch]
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2014-11-11 A few little things to do on full Eagle
    [Arm Board V4.brd]
2014-11-12 Implemented PoRN and Switched Power Connectors
    Implemented PoRN(PoRC) and switched to 3.5mm screw terminals
    [Arm Board V4.brd, Arm Board V4.sch]
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2014-11-15 Moving things to make room for motor controller
    [Arm Board V4.brd, Arm Board V4.sch]
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2014-11-18 Replaced caps on voltage regulator
    Need to be moved into place on full eagle and cleaned up a little. But
    replaced them with ones that can be purchased rather then imaginary
    ones I wished existed.
    [Arm Board V4.brd, Arm Board V4.sch]
2014-11-18 Added 1uF ceramic caps to help with ripple
    [Arm Board V4.brd, Arm Board V4.sch]
2014-11-18 Positioned all the caps correctly
    I think the board is finished but may change as I look for parts to make
    sure everything is correct
    [Arm Board V4.brd, Arm Board V4.sch]
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2014-11-19 Added a few other boards to work on
    [32u4 Xbee Shield.brd, 32u4 Xbee Shield.sch, PoRN.brd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]
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2014-11-19 Cleaned up and changed a few things on arm
    [Arm Board V4.brd]
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2014-11-20 Added headers for IMU breakout
    In addition to keeping the IMU chip on the board.
    [Arm Board V4.brd, Arm Board V4.sch]
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2014-12-13 Near finished Code for Robotic Arm
    We was able to build the code without errors for the dynamixels for the
    Robotic Arm.
    [main.c]
2014-12-17 Fixed a few things on shields
    [32u4 Drill Shield.brd, 32u4 Drill Shield.sch]
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2015-01-12 Revert "Near finished Code for Robotic Arm"
    This reverts commit c79e70b838ebad85c01b88856354583d33e78064.
    [main.c]
2015-01-12 Revert "Revert "Near finished Code for Robotic Arm""
    This reverts commit ab0c4457a740263579987729d9b1f28ad8562e1e.
    [main.c]
2015-01-12 Revert "Revert "Revert "Near finished Code for Robotic Arm"""
    This reverts commit 966fc79ac9e8e57bb9d128f49c2db74a6339a06e.
    [main.c]

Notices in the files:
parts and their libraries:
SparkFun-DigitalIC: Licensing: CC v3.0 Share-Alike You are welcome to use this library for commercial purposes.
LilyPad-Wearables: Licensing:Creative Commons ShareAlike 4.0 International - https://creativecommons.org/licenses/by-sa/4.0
